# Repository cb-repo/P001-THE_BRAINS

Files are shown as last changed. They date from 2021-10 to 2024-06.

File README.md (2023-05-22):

# THE BRAINS v4.0

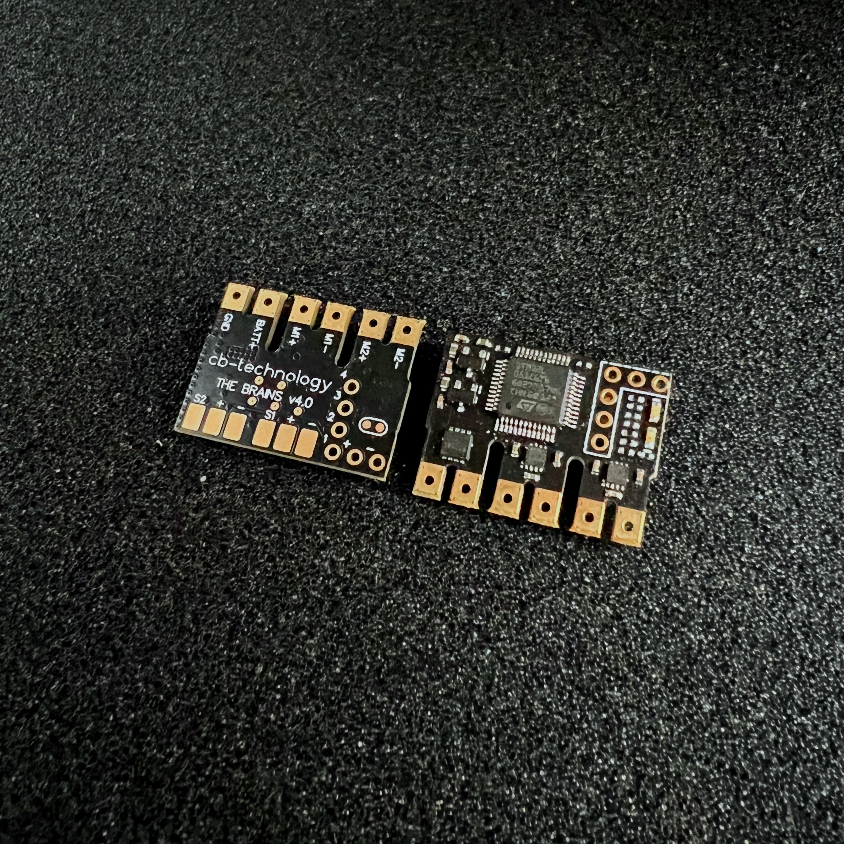
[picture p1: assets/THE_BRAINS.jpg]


THE BRAINS is an compact and lightweight dual DC-motor ESC: originally designed for antweight combat robots, but is suitable for any appliction requiring a lightweight motor driver.

Designed and built in [Christchurch, New Zealand ](https://www.google.co.nz/maps/place/Christchurch+New+Zealand) by Connor Benton, visit [cb-technology](https://www.cb-technology.co.nz/) for details.

## FEATURES

- 2x Bi-Directional DC motor outputs.
- 2x Signal output channels for additional electroncis (BLDC ESC, servo, etc).
- Status LED's to indicate run mode, faults and calibration.
- Under-voltage, over-current, over-temperature, and reverse polarity protections.
- Internal BEC to provide power to the radio reciever.
- Failsafe checks for loss of connection with radio.
- Auto-Detection of different radio protocols on the same input.
- Instant brown-out recovery.
- Calibrate function to customise drive mode, channel mapping, and channel inversion.
- Includes a 100nF capacitor across each motor to filter noise and voltage spikes.

## SPECIFICATIONS

- **Dimensions:** 25x19x3 mm
- **Weight:** 2g *excluding wires*
- **Input Voltage - Rated:** 2S lipo (6-10.4V)
- **Input Voltage - Max:** 12.0V
- **Motor Output:** 2.1A cont (3A peak) per channel 
- **BEC:** 5V, 80mA. Designed to power the radio reciever but no motors or servos
- **Signal Input:** Servo PWM, PPM, IBUS, SBUS
- **Signal Mixing:** Onboard signal mixing for TANK/ARCADE drive styles and channel mapping + inverting
- **Signal Output:** Servo PWM 
   
## Status LEDs
There are two LEDs on THE BRAINS (1x red, 1x green) and the behaviour of each indicate what state the device is in.
 - **Normal Operation** Green: ON, Red: OFF
 - **Fault Conditions**
    - **Signal-Input** Green: FLASH, Red: OFF
    - **Under-Voltage** Green: OFF, Red: FLASH (1Hz)
    - **Over-Temperature** Green: OFF, Red: FAST FLASH (5Hz)
 - **Calibration** Green: PATTERN, Red: PATTERN. (See Calibration section for specific LED patterns) 

## Fault Conditions
In all of the following fault conditions, all drive/output signals are stopped no matter the input signals. Once the fault condition is resolved, functionality will resume immediately. 
 - **Under-Voltage:** An under-voltage event occurs if the battery voltage falls below 3.2V (per cell). 
 - **Over-Temperature:** An over-temperature event occurs when the temperature sense circuit on THE BRAINS reaches 100°C.
 - **Signal-Input:** A signal-input fault occurs if the signal between the THE BRAINS and the radio reciever is lost. Note: You still need to set the failsafe on the radio reciever to detect loss of connection with the transmitter.

## Calibration
###### Calibration Parameters
THE BRAINS has a number of calibration parateters that are can be chosen from, these are:
- **Input Signal:**
At no point should the operator have to manually set the protocol, this will be auto-detected without the operator knowing.
    - Servo PWM (standard 1-2ms pulse)
    - PPM
    - IBUS
    - SBUS
- **Driving Mode:**
    - Tank (Each motor speed is controlled by a different input)
    - Arcade (One input controls both motor speeds and another is mixed in to control the steering) 
- **Signal Mapping:**
    - Any input channel can be mapped to any of the 4 outputs (2x motors + 2x signal output). 
    - Any channel can be reversed (usually auto-detected during the calibration procedure). 

The default calibration parameters are:
- **Input Signal:** SBUS
- **Driving Mode:** TANK
- **Signal Mapping:** 
     - Ch1 = Motor1, 
     - Ch2 = Motor2,
     - Ch3 = Servo1,
     - Ch4 = Servo2,

###### Calibration Procedure
 1. Ensure the transmitter is turned ON, it has been bound to the radio reciever, and all sticks are in their zero (neutral) position.

 2. Plug the radio reciever and motors into THE BRAINS. 
 It is important that the motors are connected in the orientation used for the final robot, this will allow auto-detection of the channel mapping and inversion during the following Simon-says process.

 3. Turn THE BRAINS ON and, within 10 seconds, trigger the calibration procedure using one of the following:
    - Short-circuit the two calibration pads on the underside. 
    These pads are the two circular pads close together and circled with silkscreen.
    - Wiggle any input on the transmitter back and forward 10 times. 
    Make sure to push the stick from CENTER all the way to MAX/MIN when wiggling. 

 4. Both status LEDs will pulse 10 times and then stay fully illumintaed to indicated THE BRAINS has entered CALIBRATION mode and is ready to begin the Simon-Says process. 

 5. When ready, push any stick on the transmitter to MAX and back to CENTER.
 The rest of the calibration happens pretty quickly so please read, and understand, steps 6 + 7 before proceeding. 

 6. Both status LED's will turn OFF and the Simon-says motor calibration procedure is started. 
    - Two tests are run, each will twitch the two motors and cause the robot to move forward, reverse, left, or right. 
    The user must then input that motion back into the remote. eg:
        - Robot twitches forward: Tank drive, simualtaneously push both sticks forward. Arcarde drive, push one stick forward.
        - Robot twitches left: Tank drive, simualtaneously push left stick back and right forward. Arade drive, push one stick left
    - The process for each test is:
        1. Both LED's turn OFF
        2. The motor twitches
        3. Red LED turns ON
        4. User presses input(s) to MAX/MIN
        5. Green LED turns ON 
        6. User returns input(s) back to CENTER
        7. Both LED's pulse 3 times to indicate success
        8. Repeat for second test

 7. Both status LED's will again turn OFF and the Simon-says output signal calibration procedure is started. 
    - Two more tests are run to map the inputs to the Signal 1 and 2 outputs. The primary difference with this test is that no motor are driven, THE BRAINS is just monitoring the inputs.
    - The process for each test is:
        1. Both LED's will momentrarily turn OFF to indicate the test has started
        2. Red LED turns ON
        3. User presses the input (to MAX/MIN) they want mapped to output signal 1
        4. Green LED turns ON
        5. User returns input back to CENTER 
        6. Both LED's pulse 3 times to indicate success
        7. Repeat for output signal 2.

 12. Calibration Complete
     - Both status LEDs will pulse 10 times to indicate a successfull calibration.
     - Once the LED pulses are complete, THE BRAINS immediately enter Run mode with the new calibration.
     - If THE BRAINS is turned OFF before completing the calibration process, NONE of the new parameters are stored and it will revert to the previous configuraion.

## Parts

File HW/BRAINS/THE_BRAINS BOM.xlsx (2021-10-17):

 |  |  | InFact Ltd.
 |  |  | 5 Amuri Park
 |  |  | 404 Barbadoes Street
 |  |  | Christchurch 8013
 |  |  | New Zealand
 |  | www.infact.co.nz
Bill of Materials |  |  | PXXX-50X - Description
Line | Manufacturer | Manufacturer Part Number | Description | Supplier 1 | Supplier Part Number 1 | Unit Price | Qty | Cost | Ordered | Received | Designator
1 | STMicroelectronics | STM32L051C6T6 | IC MCU 32BIT 32KB FLASH 48LQFP | Digi-Key | 497-15202-ND | $4.82 | 1 | $4.82 | Y | Y | U4
2 | STMicroelectronics | LDL212PUR | IC REG LINEAR POS ADJ 1.2A 6DFN | Digi-Key | 497-16566-1-ND | $0.58 | 1 | $0.58 | Y | Y | U2
3 | Texas Instruments | DRV8837CDSGR | IC HALF-BRIDGE DRVR PWM 8WSON | Digi-Key | 296-47205-1-ND | $1.21 | 2 | $2.42 | Y | Y | U6, U7
4 | Rohm Semiconductor | RQ3E120ATTB | MOSFET P-CH 30V 12A 8HSMT | Digi-Key | RQ3E120ATTBCT-ND | $0.90 | 1 | $0.90 | Y | Y
5 | Murata Electronics North America | BLM15HG102SN1D | FILTER CHIP 1000 OHM 250MA 0402 | Digi-Key | 490-3999-1-ND | $0.06 | 1 | $0.06 |  |  | L1
6 | Stackpole Electronics Inc | CSR0402FKR100 | RES 0.1 OHM 1% 1/8W 0402 | Digi-Key | CSR0402FKR100CT-ND | $0.18 | 1 | $0.18 | Y |  | R2
7 | Samsung Electro-Mechanics | CL21A106KAYNNNG | CAP CER 10UF 25V X5R 0805 | Digi-Key | 1276-6454-1-ND | $0.11 | 1 | $0.11 | Y |  | C7
8 | Bourns Inc. | MF-FSMF020X-2 | PTC RESET FUSE 9V 200MA 0603 | Digi-Key | MF-FSMF020X-2CT-ND | $0.50 | 1 | $0.50 | Y |  | R4
9 | Taiyo Yuden | UMK105CBJ105MV-F | CAP CER 1UF 50V X5R 0402 | Digi-Key | 587-6278-1-ND | $0.16 | 2 | $0.33 | Y | Y | C8, C4
10 | KYOCERA AVX | 0402YD475MAT2A | CAP CER 4.7UF 16V X5R 0402 | Digi-Key | 478-10788-1-ND | $0.18 | 1 | $0.18 | Y | Y | C12
11 | Taiyo Yuden | UMK105B7104KV-FR | CAP CER 0.1UF 50V X7R 0402 | Digi-Key | 587-3498-1-ND | $0.05 | 12 | $0.60 | Y | Y | C1, C2, C6, C9, C10, C11, C13, C15, C18, C19, C20, C21
12 | Lumex Opto/Components Inc | SML-LX0603GW-TR | LED 565NM GRN DIFF 0603 SMD | Digi-Key | 67-1549-1-ND | $0.23 | 1 | $0.23 | Y | Y | DS2
13 | Lumex Opto/Components Inc | SML-LX0603IW-TR | LED 635NM RED DIFF 0603 SMD | Digi-Key | 67-1548-1-ND | $0.23 | 1 | $0.23 | Y | Y | DS1
14 | Vishay Dale | CRCW04021K80FKED | RES 1k8 0.0625W 1% 0402 SMD | Digi-Key | 541-1.80KLCT-ND | $0.01 | 1 | $0.01 | Y | Y | R8
15 | Yageo | RC0402FR-0710KL | RES 10K OHM 1/16W 1% 0402 SMD | Digi-Key | 311-10.0KLRCT-ND | $0.00385 | 7 | $0.03 | Y | Y | R7, R9, R10, R11, R12, R13, R14
16 | Yageo | RC0402FR-07120RL | RES 120 OHM 1/16W 0402 SMD | Digi-Key | 311-120LRCT-ND | $0.00385 | 2 | $0.01 | Y | Y | R5, R15
17 | Yageo | RC0402FR-07150KL | RES SMD 150K OHM 1% 1/16W 0402 | Digi-Key | 311-150KLRCT-ND | $0.01 | 1 | $0.01 | Y | Y | R3
18 | Yageo | RC0402FR-07270KL | RES SMD 270K OHM 1% 1/16W 0402 | Digi-Key | 311-270KLRCT-ND | $0.01 | 1 | $0.01 | Y | Y | R1
19 | JLC PCB |  | PCB |  |  | $2.62 | 1 | $2.62 | Y
20 | Chip Quik Inc. | SMD291AX50T3 | SLDR PASTE NO-CLN SN63/PB37 50G | Digi-Key | SMD291AX50T3-ND | $0.21 | 1 | $0.21 | Y | Y
 |  |  |  |  |  |  | 31 | $14.02
Approved |  |  | Notes
 | Total Order Cost
 | Total Order QTY | 60
 | Unit Cost | $14.02
 | Unit Sell Price | 30
 | Unit Profit | 15.98304
 | Total Profit | 958.9824

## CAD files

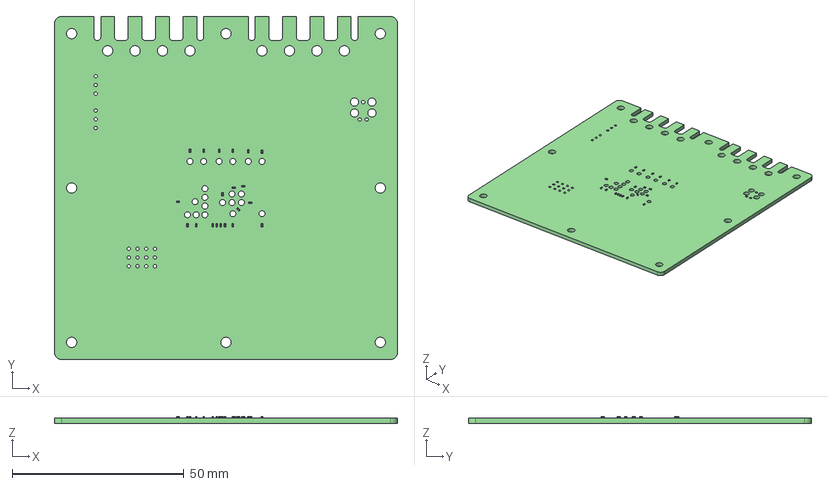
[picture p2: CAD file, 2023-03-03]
FIXTURE/outputs/TEST_FIXTURE.step
100.0 x 100.0 x 1.95 mm
TEST_FIXTURE PCB

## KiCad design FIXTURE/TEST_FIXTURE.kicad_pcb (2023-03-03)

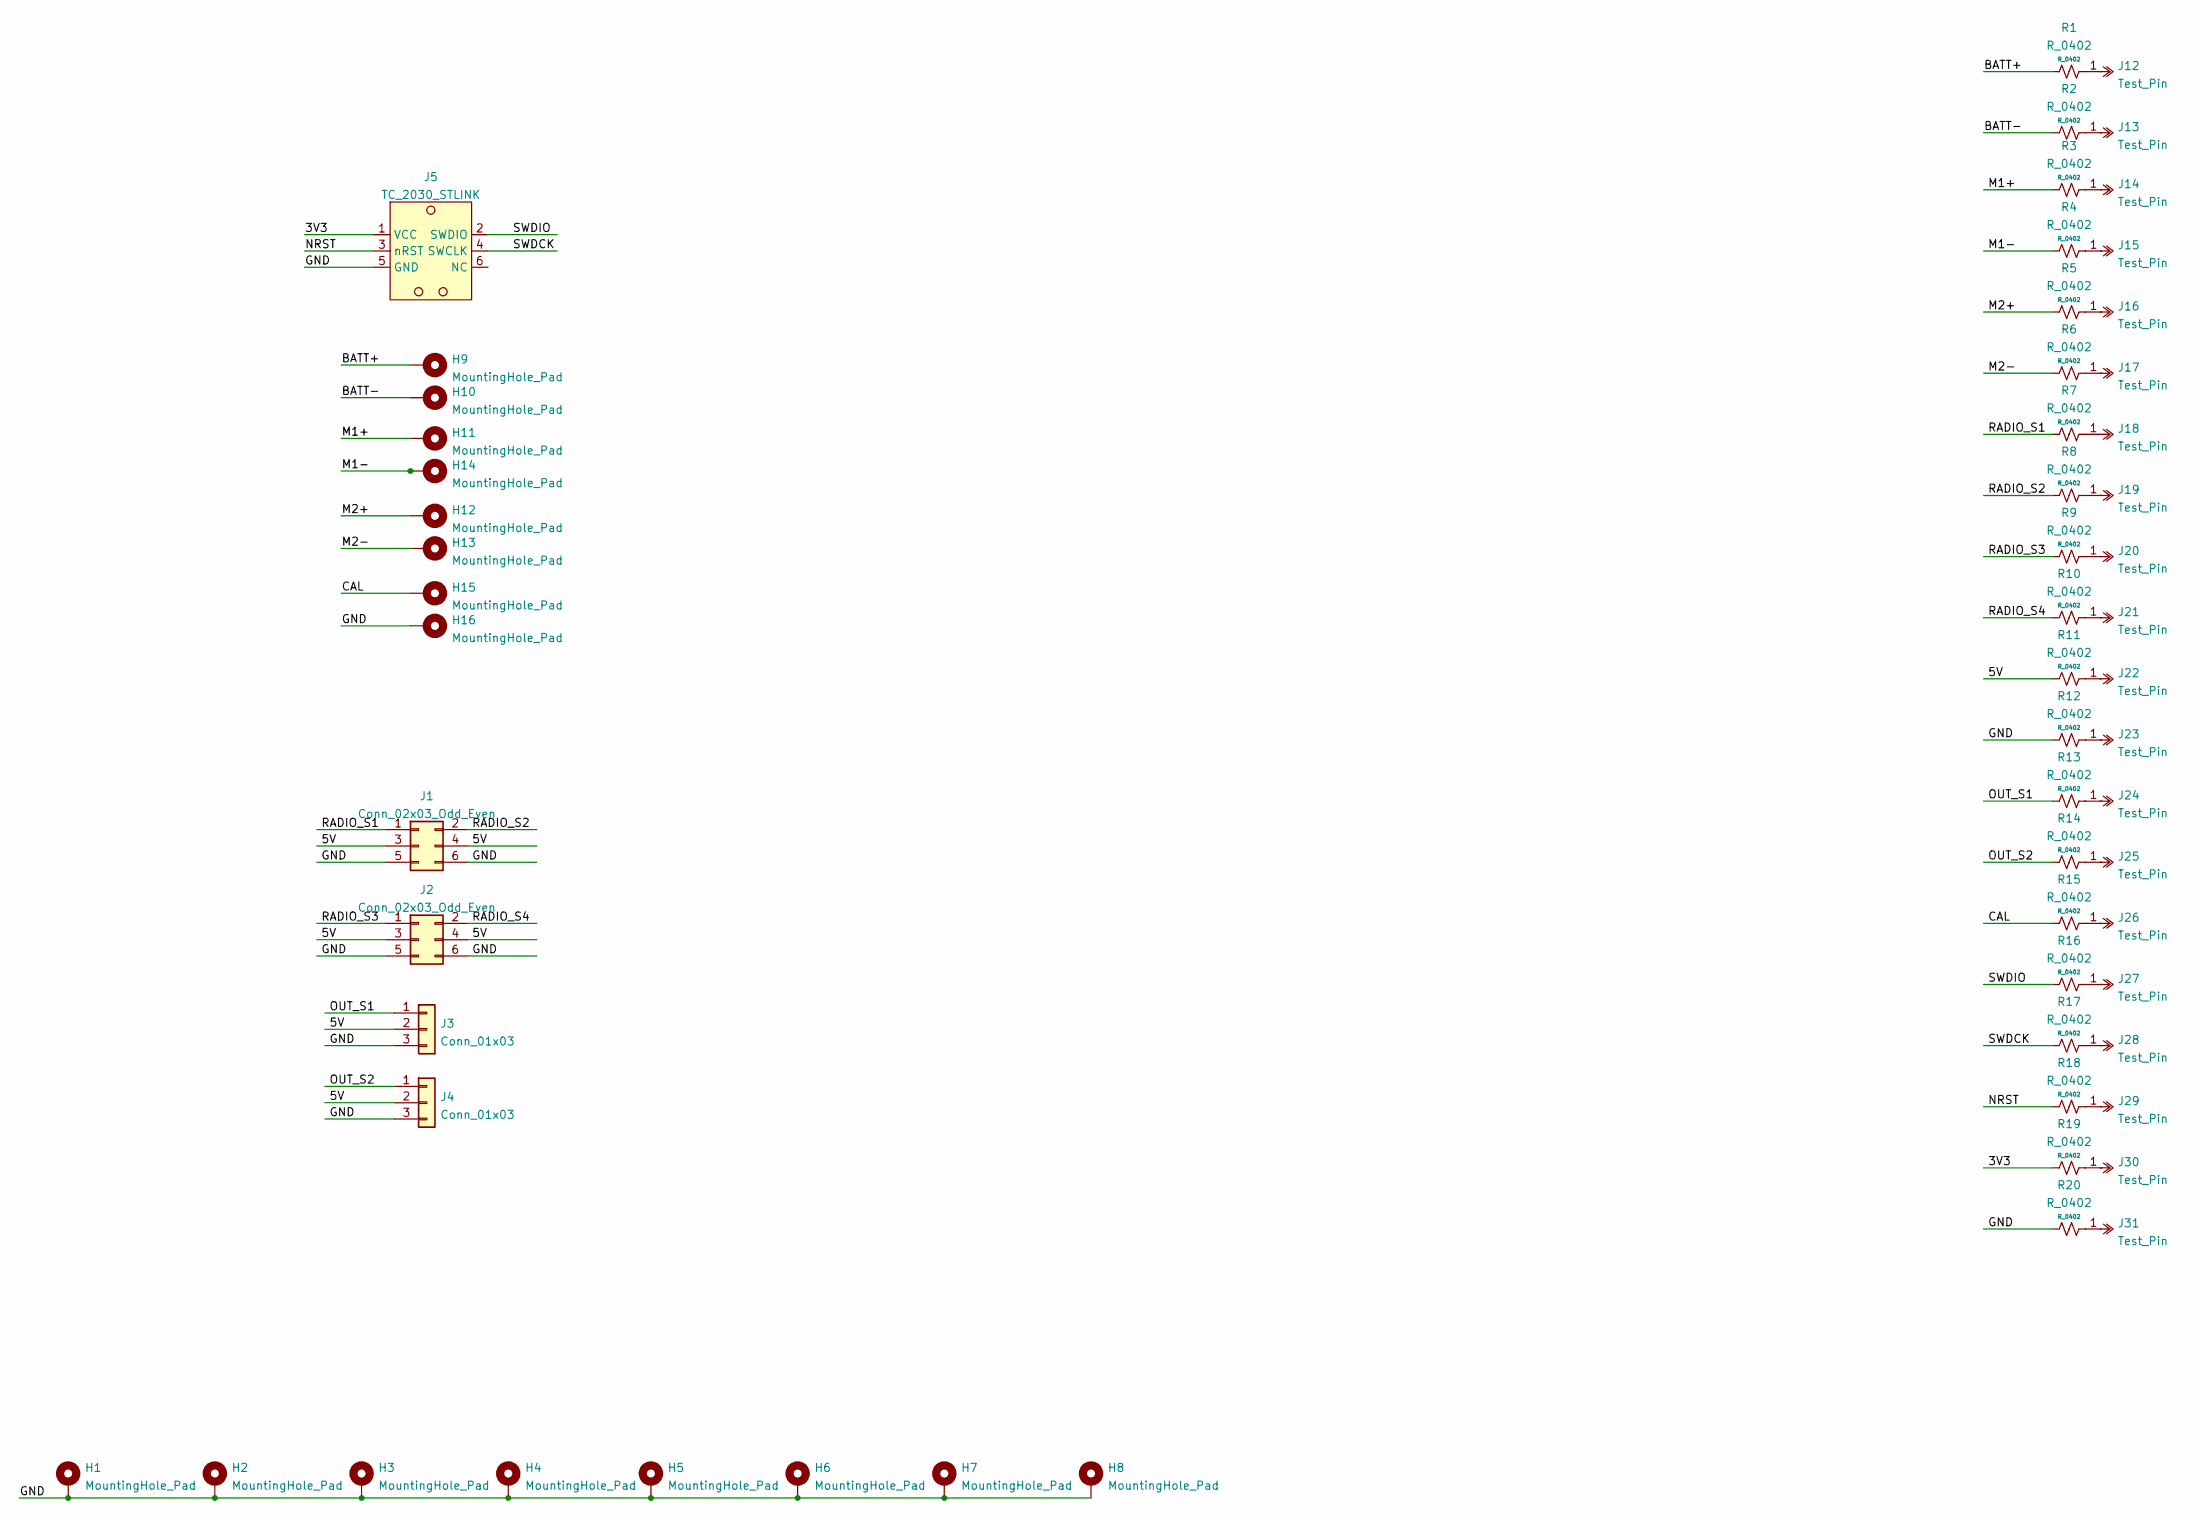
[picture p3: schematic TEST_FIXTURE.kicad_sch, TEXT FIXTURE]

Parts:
H1, H2, H3, H4, H5, H6, H7, H8, H9, H10, H11, H12, H13, H14, H15, H16: MountingHole_Pad; MountingHole_3mm_Pad_TopBottom
J1, J2: Conn_02x03_Odd_Even; PinHeader_2x03_P2.54mm_Vertical
J3, J4: Conn_01x03; PinHeader_1x03_P2.54mm_Horizontal
J5: TC_2030_STLINK; Tag-Connect_TC2030-IDC-FP_2x03_P1.27mm_Vertical
J12, J13, J14, J15, J16, J17, J18, J19, J20, J21, J22, J23, J24, J25, J26, J27, J28, J29, J30, J31: Test_Pin; R-2-SC
R1, R2, R3, R4, R5, R6, R7, R8, R9, R10, R11, R12, R13, R14, R15, R16, R17, R18, R19, R20: R_0402

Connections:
/3V3: J5.1 (VCC), R19.1
/5V: J1.3, J1.4, J2.3, J2.4, J3.2, J4.2, R11.1
/BATT+: H9.1, R1.1
/BATT-: H10.1, R2.1
/CAL: H15.1, R15.1
/GND: H1.1, H2.1, H3.1, H4.1, H5.1, H6.1, H7.1, H8.1, H16.1, J1.5, J1.6, J2.5, J2.6, J3.3, J4.3, J5.5 (GND), R12.1, R20.1
/M1+: H11.1, R3.1
/M1-: H14.1, R4.1
/M2+: H12.1, R5.1
/M2-: H13.1, R6.1
/NRST: J5.3 (nRST), R18.1
/OUT_S1: J3.1, R13.1
/OUT_S2: J4.1, R14.1
/RADIO_S1: J1.1, R7.1
/RADIO_S2: J1.2, R8.1
/RADIO_S3: J2.1, R9.1
/RADIO_S4: J2.2, R10.1
/SWDCK: J5.4 (SWCLK), R17.1
/SWDIO: J5.2 (SWDIO), R16.1
unnamed: J12.1, R1.2
unnamed: J13.1, R2.2
unnamed: J14.1, R3.2
unnamed: J15.1, R4.2
unnamed: J16.1, R5.2
unnamed: J17.1, R6.2
unnamed: J18.1, R7.2
unnamed: J19.1, R8.2
unnamed: J20.1, R9.2
unnamed: J21.1, R10.2
unnamed: J22.1, R11.2
unnamed: J23.1, R12.2
unnamed: J24.1, R13.2
unnamed: J25.1, R14.2
unnamed: J26.1, R15.2
unnamed: J27.1, R16.2
unnamed: J28.1, R17.2
unnamed: J29.1, R18.2
unnamed: J30.1, R19.2
unnamed: J31.1, R20.2

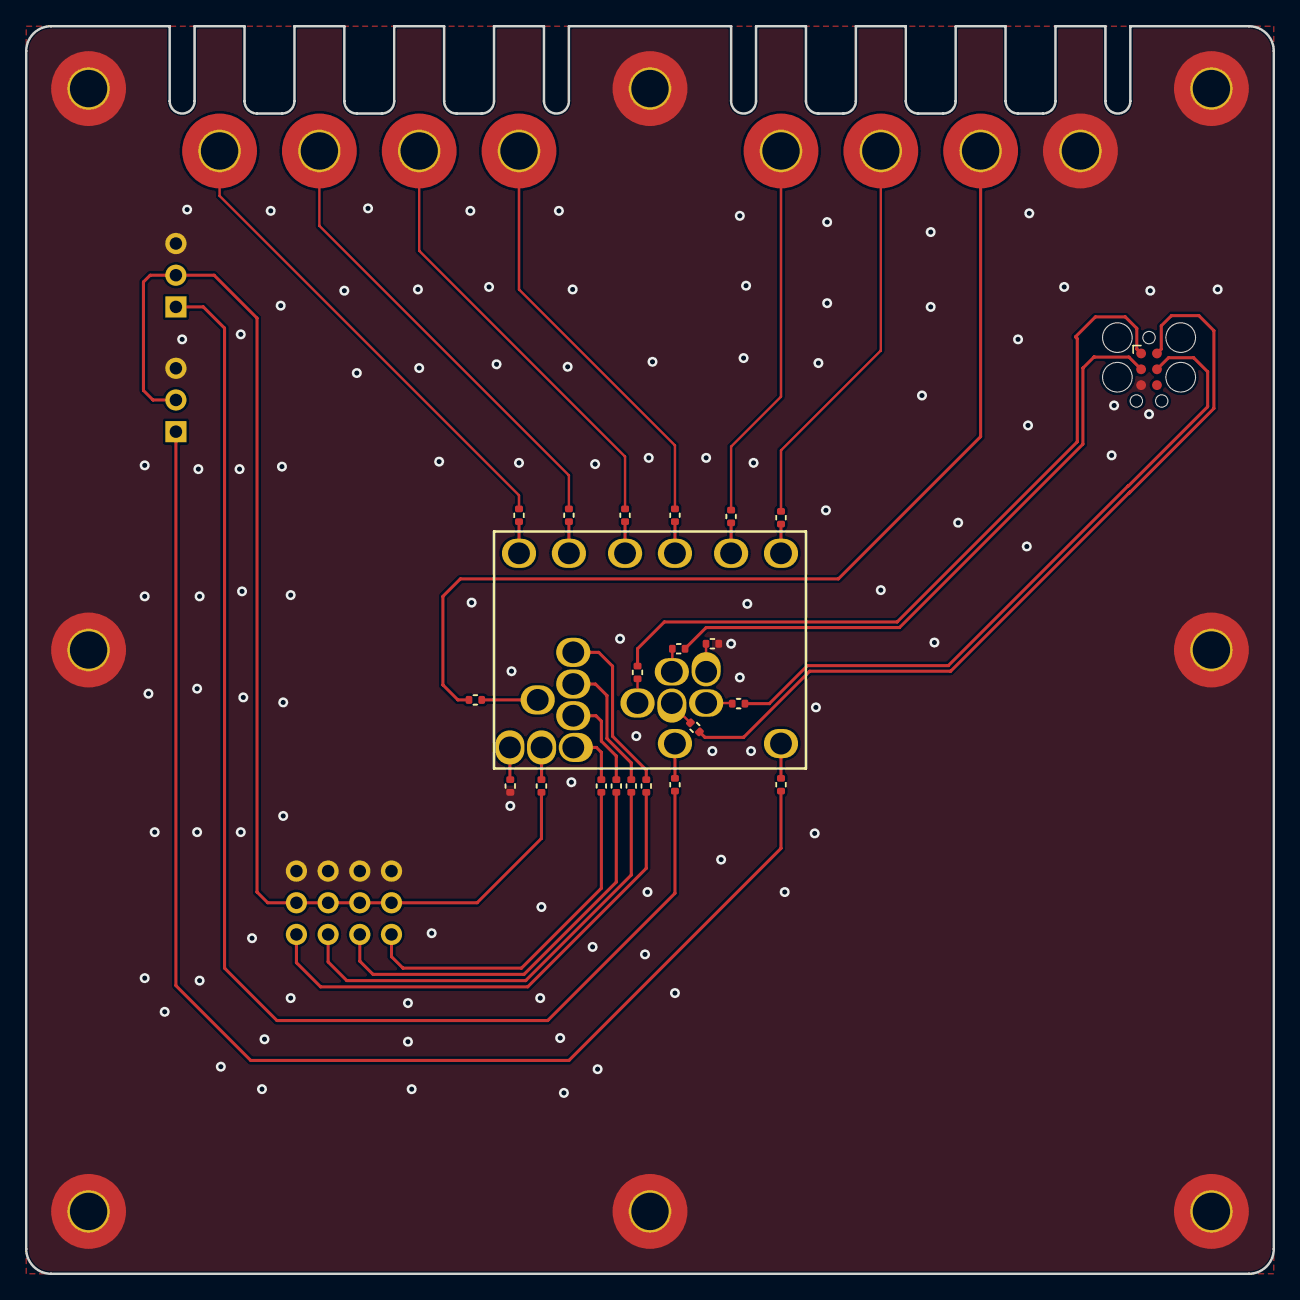
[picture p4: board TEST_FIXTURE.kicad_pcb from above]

Board: 2 copper layers, 100.0 x 100.0 mm, 61 parts (0 on the bottom side), 39 nets.

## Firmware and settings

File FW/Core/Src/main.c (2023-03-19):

/* ~~~~~~~~~~~~~~~~~~~~~~~~~~~~~~~~~~~~~~~~~~~~~~~~~~ */

#include "Core.h"
#include "Radio.h"
#include "System.h"
#include "Motor.h"
#include "Servo.h"
#include "US.h"

/*
 * PRIVATE DEFINITIONS
 */

/*
 * PRIVATE TYPES
 */

/*
 * PRIVATE PROTOTYPES
 */

/*
 * PRIVATE VARIABLES
 */

/*
 * PUBLIC FUNCTIONS
 */

int main (void)
{
 	CORE_Init();
	SYSTEM_Init();
	MOTOR_Init();

	CORE_Idle();

	while (1)
	{
		SYSTEM_Update();

		CORE_Idle();
	}
}

/*
 * PRIVATE FUNCTIONS
 */

/*
 * INTERRUPT ROUTINES
 */

/* ~~~~~~~~~~~~~~~~~~~~~~~~~~~~~~~~~~~~~~~~~~~~~~~~~~ */

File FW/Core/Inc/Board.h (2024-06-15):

/* ~~~~~~~~~~~~~~~~~~~~~~~~~~~~~~~~~~~~~~~~~~~~~~~~~~ */
#ifndef BOARD_H
#define BOARD_H
/* ~~~~~~~~~~~~~~~~~~~~~~~~~~~~~~~~~~~~~~~~~~~~~~~~~~ */


#define STM32L0

// ADC CONFIG
#define ADC_VREF	      	3300

//#define DATA_EEPROM_BASE

// TIM CONFIG
#define TIM_USE_IRQS
// 		Motor O/P
#define TIM2_ENABLE
#define TIM_MOTOR 			TIM_2
#define TIM_MOTOR_AF2		GPIO_AF2_TIM2
#define TIM_MOTOR_RELOAD 	255
#define TIM_MOTOR_FREQ		(MOTOR_FREQ*(TIM_MOTOR_RELOAD+1))
// 		Radio I/P
#define TIM6_ENABLE
#define TIM_RADIO 			TIM_6
#define TIM_RADIO_RELOAD 	0xffff
#define TIM_RADIO_FREQ		1000000
#define PWM_TIM				TIM_RADIO
#define PWM_TIM_FREQ		TIM_RADIO_FREQ
#define PWM_TIM_RELOAD		TIM_RADIO_RELOAD
#define PPM_TIM				TIM_RADIO
#define PPM_TIM_FREQ		TIM_RADIO_FREQ
#define PPM_TIM_RELOAD		TIM_RADIO_RELOAD
// 		Servo1 O/P
#define TIM21_ENABLE
#define TIM_SERVO1 			TIM_21
#define TIM_SERVO1_RELOAD 	(10*1000)
#define TIM_SERVO1_FREQ		1000000
// 		Servo2 O/P
#define TIM22_ENABLE
#define TIM_SERVO2 			TIM_22
#define TIM_SERVO2_RELOAD 	(10*1000)
#define TIM_SERVO2_FREQ		1000000


// UART CONFIG
//		LPUART1_Tx - Pin21 (PB10) -- Not Using Tx Function
//		LPUART1_Rx - Pin22 (PB11)
#define SBUS_UART			UART_LP
#define IBUS_UART			UART_LP
#define RADIO_UART			UART_LP
#define RADIO_UART_GPIO		UARTLP_GPIO
#define RADIO_UART_PIN		UARTLP_PINS
#define UARTLP_GPIO			GPIOB
#define UARTLP_PINS			GPIO_PIN_11 // (GPIO_PIN_10 | GPIO_PIN_11)
#define UARTLP_AF		    GPIO_AF4_LPUART1
#define UART_BFR_SIZE     	256


// IRQ CONFIG
#define GPIO_USE_IRQS
#define GPIO_IRQ2_ENABLE
#define GPIO_IRQ5_ENABLE
#define GPIO_IRQ6_ENABLE
#define GPIO_IRQ10_ENABLE
#define GPIO_IRQ11_ENABLE
// 		Calibrate I/P - Pin21 (PB10)
#define CALIBRATE_GPIO		GPIOB
#define	CALIBRATE_PIN		GPIO_PIN_10
// 		RadioS1 - Pin22 (PB11)
#define PWM_S1_GPIO		GPIOB
#define PWM_S1_PIN		GPIO_PIN_11
// 		RadioS2 - Pin20 (PB2)
#define PWM_S2_GPIO		GPIOB
#define PWM_S2_PIN		GPIO_PIN_2
// 		RadioS3 - Pin16 (PA6)
#define PWM_S3_GPIO		GPIOA
#define PWM_S3_PIN		GPIO_PIN_6
// 		RadioS4 - Pin15 (PA5)
#define PWM_S4_GPIO		GPIOA
#define PWM_S4_PIN		GPIO_PIN_5

#define PPM_GPIO		PWM_S1_GPIO
#define PPM_PIN			PWM_S1_PIN


// DC-MOTOR CONFIG
#define USE_DRV8212			true
#define USE_DRV8837			false
#define MOTOR_LPWM1_CH		0
#define MOTOR_LPWM2_CH		1
#define MOTOR_RPWM1_CH		2
#define MOTOR_RPWM2_CH		3
// 		MotorL_PWM1 - Pin10 (PA0)
#define MOTOR_LPWM1_GPIO	GPIOA
#define MOTOR_LPWM1_PIN		GPIO_PIN_0
// 		MotorL_PWM2 - Pin11 (PA1)
#define MOTOR_LPWM2_GPIO	GPIOA
#define MOTOR_LPWM2_PIN		GPIO_PIN_1
// 		MotorL_MODE - Pin4 (PC15)
#define MOTOR_LMODE_GPIO	GPIOC
#define MOTOR_LMODE_PIN		GPIO_PIN_15
// 		MotorR_PWM1 - Pin12 (PA2)
#define MOTOR_RPWM1_GPIO	GPIOA
#define MOTOR_RPWM1_PIN		GPIO_PIN_2
// 		MotorR_PWM2 - Pin13 (PA3)
#define MOTOR_RPWM2_GPIO	GPIOA
#define MOTOR_RPWM2_PIN		GPIO_PIN_3
// 		MotorR_MODE - Pin14 (PA4)
#define MOTOR_RMODE_GPIO	GPIOA
#define MOTOR_RMODE_PIN		GPIO_PIN_4


// IO CONFIG
// 		Servo1 O/P - Pin25 (PB12)
#define SERVO1_GPIO			GPIOB
#define SERVO1_PIN			GPIO_PIN_12
// 		Servo2 O/P - Pin13 (PA15)
#define SERVO2_GPIO			GPIOA
#define SERVO2_PIN			GPIO_PIN_15
// 		Battery Detect - Pin17 (PA7)
#define BATTERY_GPIO		GPIOA
#define	BATTERY_PIN			GPIO_PIN_7
#define BATTERY_CHANNEL		ADC_Channel_7
#define BATTERY_DET_RLOW	18
#define BATTERY_DET_RHIGH	100
// 		Status/Green LED - Pin19 (PB1)
#define LED_STATUS_GPIO		GPIOB
#define LED_STATUS_PIN		GPIO_PIN_1
// 		Fault/Red LED - Pin18 (PB0)
#define LED_FAULT_GPIO		GPIOB
#define LED_FAULT_PIN		GPIO_PIN_0


#endif /* BOARD_H */
/* ~~~~~~~~~~~~~~~~~~~~~~~~~~~~~~~~~~~~~~~~~~~~~~~~~~ */

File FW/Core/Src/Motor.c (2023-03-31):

/* ~~~~~~~~~~~~~~~~~~~~~~~~~~~~~~~~~~~~~~~~~~~~~~~~~~ */

#include "Motor.h"
#include "GPIO.h"
#include "TIM.h"

/*
 * PRIVATE DEFINITIONSb
 */

#define MOTOR_BRAKE		1

#if USE_DRV8212
#define MODE_PWM		GPIO_PIN_RESET
#define MODE_COAST		GPIO_PIN_RESET
#define MODE_BRAKE		GPIO_PIN_RESET
#define PWM_COAST		MOTOR_OFF
#define PWM_BRAKE 		MOTOR_MAX
#elif USE_DRV8837
#define MODE_PWM		GPIO_PIN_SET
#define MODE_COAST		GPIO_PIN_SET
#define MODE_BRAKE		GPIO_PIN_SET
#define PWM_COAST		MOTOR_OFF
#define PWM_BRAKE 		MOTOR_MAX
#endif

/*
 * PRIVATE TYPES
 */


/*
 * PRIVATE PROTOTYPES
 */

void MOTOR_M1_Brake (void);
void MOTOR_M2_Brake (void);
void MOTOR_M1_Coast (void);
void MOTOR_M2_Coast (void);

void MOTOR_M1_Update (int32_t);
void MOTOR_M2_Update (int32_t);

/*
 * PRIVATE VARIABLES
 */


/*
 * PUBLIC FUNCTIONS
 */

void MOTOR_Init (void)
{
	TIM_Init(TIM_MOTOR, TIM_MOTOR_FREQ, TIM_MOTOR_RELOAD);

#if defined(USE_DRV8212)
	GPIO_EnableOutput(MOTOR_LMODE_GPIO, MOTOR_LMODE_PIN, MODE_PWM);
	GPIO_EnableOutput(MOTOR_RMODE_GPIO, MOTOR_RMODE_PIN, MODE_PWM);
#endif

	TIM_EnablePwm(TIM_MOTOR, MOTOR_LPWM1_CH, MOTOR_LPWM1_GPIO, MOTOR_LPWM1_PIN, TIM_MOTOR_AF2);
	TIM_EnablePwm(TIM_MOTOR, MOTOR_LPWM2_CH, MOTOR_LPWM2_GPIO, MOTOR_LPWM2_PIN, TIM_MOTOR_AF2);
	TIM_EnablePwm(TIM_MOTOR, MOTOR_RPWM1_CH, MOTOR_RPWM1_GPIO, MOTOR_RPWM1_PIN, TIM_MOTOR_AF2);
	TIM_EnablePwm(TIM_MOTOR, MOTOR_RPWM2_CH, MOTOR_RPWM2_GPIO, MOTOR_RPWM2_PIN, TIM_MOTOR_AF2);

	MOTOR_Update(MOTOR_OFF, MOTOR_OFF);
	TIM_Start(TIM_MOTOR);
}


void MOTOR_Update (int32_t M1, int32_t M2)
{
	MOTOR_M1_Update(M1);
	MOTOR_M2_Update(M2);
}

/*
 * PRIVATE FUNCTIONS
 */

void MOTOR_M1_Brake (void)
{
	GPIO_Write(MOTOR_LMODE_GPIO, MOTOR_LMODE_PIN, MODE_BRAKE);
	TIM_SetPulse(TIM_MOTOR, MOTOR_LPWM1_CH, PWM_BRAKE);
	TIM_SetPulse(TIM_MOTOR, MOTOR_LPWM2_CH, PWM_BRAKE);
}

void MOTOR_M2_Brake (void)
{
	GPIO_Write(MOTOR_RMODE_GPIO, MOTOR_RMODE_PIN, MODE_BRAKE);
	TIM_SetPulse(TIM_MOTOR, MOTOR_RPWM1_CH, PWM_BRAKE);
	TIM_SetPulse(TIM_MOTOR, MOTOR_RPWM2_CH, PWM_BRAKE);
}

void MOTOR_M1_Coast(void)
{
	GPIO_Write(MOTOR_LMODE_GPIO, MOTOR_LMODE_PIN, MODE_COAST);
	TIM_SetPulse(TIM_MOTOR, MOTOR_LPWM1_CH, PWM_COAST);
	TIM_SetPulse(TIM_MOTOR, MOTOR_LPWM2_CH, PWM_COAST);
}

void MOTOR_M2_Coast(void)
{
	GPIO_Write(MOTOR_RMODE_GPIO, MOTOR_RMODE_PIN, MODE_COAST);
	TIM_SetPulse(TIM_MOTOR, MOTOR_RPWM1_CH, PWM_COAST);
	TIM_SetPulse(TIM_MOTOR, MOTOR_RPWM2_CH, PWM_COAST);
}

void MOTOR_M1_Update (int32_t throttle)
{
	bool reverse = false;

	// Check if reversing
	if (throttle < MOTOR_OFF) {
		reverse = true;
		throttle = -throttle;
	}

	// Clamp maximum speed
	if (throttle > MOTOR_MAX) {
		throttle = MOTOR_MAX;
	}

	if ( throttle <= ( MOTOR_OFF + MOTOR_STALL ) ) {
		if (MOTOR_BRAKE) {
			MOTOR_M1_Brake();
		} else {
			MOTOR_M1_Coast();
		}
	}
	else
	{
		if ( throttle >= (MOTOR_MAX - MOTOR_MAX_THRESH ) ) {
			throttle = MOTOR_MAX;
		}

		if (reverse) {
			TIM_SetPulse(TIM_MOTOR, MOTOR_LPWM1_CH, 0);
			TIM_SetPulse(TIM_MOTOR, MOTOR_LPWM2_CH, throttle);
		} else {
			TIM_SetPulse(TIM_MOTOR, MOTOR_LPWM1_CH, throttle);
			TIM_SetPulse(TIM_MOTOR, MOTOR_LPWM2_CH, 0);
		}
	}
}

void MOTOR_M2_Update (int32_t throttle)
{
	bool reverse = false;

	// Check if reversing
	if (throttle < 0) {
		reverse = true;
		throttle = -throttle;
	}

	// Clamp maximum speed
	if (throttle > MOTOR_MAX) {
		throttle = MOTOR_MAX;
	}

	if (throttle <= MOTOR_OFF + MOTOR_STALL) {
		if (MOTOR_BRAKE) {
			MOTOR_M2_Brake();
		} else {
			MOTOR_M2_Coast();
		}
	}
	else
	{
		if ( throttle >= (MOTOR_MAX - MOTOR_MAX_THRESH ) ) {
			throttle = MOTOR_MAX;
		}

		if (reverse) {
			TIM_SetPulse(TIM_MOTOR, MOTOR_RPWM1_CH, 0);
			TIM_SetPulse(TIM_MOTOR, MOTOR_RPWM2_CH, throttle);
		} else {
			TIM_SetPulse(TIM_MOTOR, MOTOR_RPWM1_CH, throttle);
			TIM_SetPulse(TIM_MOTOR, MOTOR_RPWM2_CH, 0);
		}
	}
}

/*
 * INTERRUPT ROUTINES
 */

/* ~~~~~~~~~~~~~~~~~~~~~~~~~~~~~~~~~~~~~~~~~~~~~~~~~~ */

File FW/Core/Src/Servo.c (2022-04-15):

/* ~~~~~~~~~~~~~~~~~~~~~~~~~~~~~~~~~~~~~~~~~~~~~~~~~~ */

#include "Servo.h"
#include "GPIO.h"
#include "TIM.h"

/*
 * PRIVATE DEFINITIONS
 */

/*
 * PRIVATE TYPES
 */

/*
 * PRIVATE PROTOTYPES
 */

void SERVO_S1_Update(uint16_t offset);
void SERVO_S2_Update(uint16_t offset);

static void SERVO1_TimerReloadISR(void);
static void SERVO1_TimerPulseISR(void);
static void SERVO2_TimerReloadISR(void);
static void SERVO2_TimerPulseISR(void);

/*
 * PRIVATE VARIABLES
 */

/*
 * PUBLIC FUNCTIONS
 */

void SERVO_Init(void)
{
	GPIO_EnableOutput(SERVO1_GPIO, SERVO1_PIN, GPIO_PIN_RESET);
	TIM_Init(TIM_SERVO1, TIM_SERVO1_FREQ, TIM_SERVO1_RELOAD);
	TIM_OnReload(TIM_SERVO1, SERVO1_TimerReloadISR);
	TIM_OnPulse(TIM_SERVO1, 0, SERVO1_TimerPulseISR);
	SERVO_S1_Update(0);
	TIM_Start(TIM_SERVO1);

	GPIO_EnableOutput(SERVO2_GPIO, SERVO2_PIN, GPIO_PIN_RESET);
	TIM_Init(TIM_SERVO2, TIM_SERVO2_FREQ, TIM_SERVO2_RELOAD);
	TIM_OnReload(TIM_SERVO2, SERVO2_TimerReloadISR);
	TIM_OnPulse(TIM_SERVO2, 0, SERVO2_TimerPulseISR);
	SERVO_S2_Update(0);
	TIM_Start(TIM_SERVO2);
}

void SERVO_Deinit(void)
{
	TIM_Stop(TIM_SERVO1);
	TIM_Deinit(TIM_SERVO1);
	GPIO_Write(SERVO1_GPIO, SERVO1_PIN, GPIO_PIN_RESET);

	TIM_Stop(TIM_SERVO2);
	TIM_Deinit(TIM_SERVO2);
	GPIO_Write(SERVO2_GPIO, SERVO2_PIN, GPIO_PIN_RESET);
}

void SERVO_Update(uint16_t S1, uint16_t S2)
{
	SERVO_S1_Update(S1);
	SERVO_S2_Update(S2);
}

/*
 * PRIVATE FUNCTIONS
 */

void SERVO_S1_Update(uint16_t pulse)
{
	TIM_SetPulse(TIM_SERVO1, 0, pulse);
}

void SERVO_S2_Update(uint16_t pulse)
{
	TIM_SetPulse(TIM_SERVO2, 0, pulse);
}

/*
 * INTERRUPT ROUTINES
 */

static void SERVO1_TimerReloadISR(void)
{
	GPIO_Set(SERVO1_GPIO, SERVO1_PIN);
}

static void SERVO1_TimerPulseISR(void)
{
	GPIO_Reset(SERVO1_GPIO, SERVO1_PIN);
}

static void SERVO2_TimerReloadISR(void)
{
	GPIO_Set(SERVO2_GPIO, SERVO2_PIN);
}

static void SERVO2_TimerPulseISR(void)
{
	GPIO_Reset(SERVO2_GPIO, SERVO2_PIN);
}

/* ~~~~~~~~~~~~~~~~~~~~~~~~~~~~~~~~~~~~~~~~~~~~~~~~~~ */

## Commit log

2021-10-14 v3.0 manufacturing release files
    [BRAINS - Bill of Materials - SINGLE-BRAINS(Default).xlsx, BRAINS(Default).step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]
2021-10-17 Added v3.0 BOM File
    [THE_BRAINS BOM.xlsx]
2021-10-17 Merged Hardware and Firmware repo
    [BRAINS - Bill of Materials - SINGLE-BRAINS(Default).xlsx, BRAINS(Default).step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]
2021-10-23 Sync file structure
    [BRAINS - Bill of Materials - SINGLE-BRAINS(Default).xlsx, BRAINS(Default).step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]
2021-10-27 Updated motor functions
    Added config for different DRV drivers.
2021-11-09 Re-Integrate FW + HW
    [THE_BRAINS_FIXTURE-B_Cu.gbr, THE_BRAINS_FIXTURE-B_Mask.gbr, THE_BRAINS_FIXTURE-B_Paste.gbr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]
2021-11-10 Fixed MotorM1 AF Issue
    [BRAINS.PrjPCB]
2021-11-13 Add STM32 Lambosaurus Lib as submodule
2021-11-13 Update STM32 hal Lib
2022-01-23 Fixture PCB Upload
    [04062-Mechanical+Push+Touch+Latch.STEP, Assembly.SLDASM, BRAINS(Default).step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]
2022-04-15 Sync Mech + HW stuff
    [BRAINS.SchDoc, ProgrammerClip.SLDPRT, ProgrammerClipBottom.3MF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]
2022-04-19 Calibration Code Working
2022-08-16 Redisign with fingers for I/O and add 5V O/P
    [BRAINS - Bill of Materials - SINGLE-BRAINS(Default).xlsx, BRAINS(Default).step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]
2022-11-15 Fix Battery Detect ADC Channel
    [Board.h]
2022-11-21 Fix Default Radio Configuration from PPM to PWM
    [System.c, System.h]
2023-02-04 Changes that were on laptop
    [04062-Mechanical+Push+Touch+Latch.STEP, Assembly.SLDASM, BRAINS(Default).step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]
2023-03-07 Fix PPM and IBUS Implementation Bugs
    [Board.h, System.c, main.c]
2023-03-07 Update Calibrate Function to Include Radio Auto-Detect
2023-03-13 Update Whole Calibration Sequence and Add Comments Throughout Module
2023-03-19 Fix Calibration Sequence Issues and Reimplement Temperature Detect
    [System.c, System.h, main.c]
2023-03-31 Implement Control For DRV8837 + Fix Motor Output Disparity
    [Board.h, Motor.c]
2023-03-31 Reduce Calibration Motor Twitch Duration
    Bots were suiciding off the desk during calibration
    [Motor.c, System.c]
2023-04-03 Fix Bug With Tank Calibration Procedure
    [Board.h, System.c]
2023-04-05 CRNZ v4.0 PCB 40-off Order
2024-06-04 Update gitignore
    [TEST_FIXTURE-B_Cu.gbr, TEST_FIXTURE-B_Mask.gbr, TEST_FIXTURE-B_Paste.gbr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]
